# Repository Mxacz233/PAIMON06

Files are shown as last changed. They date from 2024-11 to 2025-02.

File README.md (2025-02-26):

<div style="flex: 1; text-align: center;">
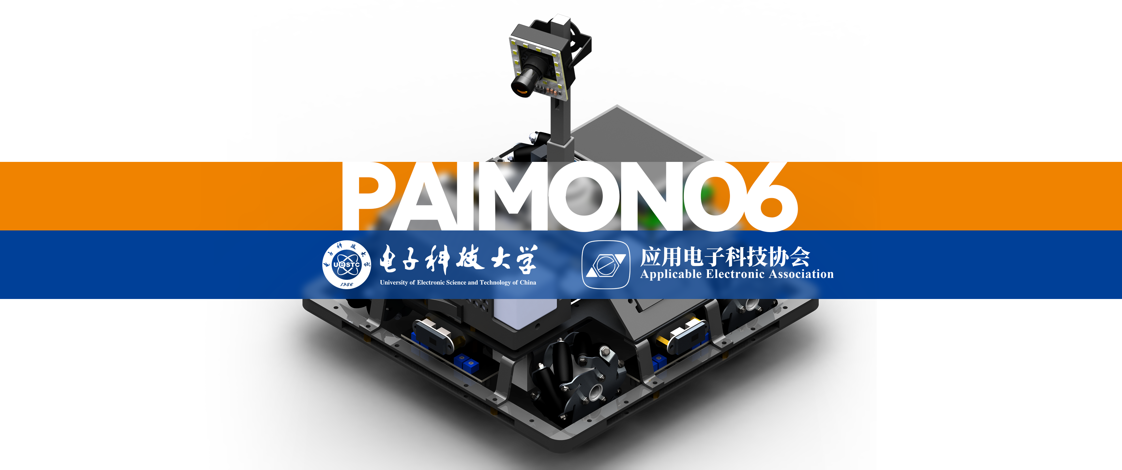
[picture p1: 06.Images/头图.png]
head
  
</div>

# PAIMON06: 高性能迷宫车










一辆全国一等奖的全部！从车上的每一颗螺丝到烧录文件的每一位HEX数据，全都在这里！

此项目是电子科技大学应用电子科技协会第十一届全国大学生光电设计竞赛（2023年）参赛作品，在西南赛区取得了第一名的成绩并在哈尔滨工业大学主办的全国总决赛中取得了全国一等奖的成绩。此项目包含了我们的全部的电路工程、全车建模、包含开发历史的软件与固件等信息。

*注意！此项目涉及嵌入式linux、嵌入式STM32、PCB设计、SolidWorks建模、Python脚本等多个领域，总文件可能较大(约650M)，建议根据需求按模块下载。*

*如果这个项目能够帮到你，请给我们一个Star⭐！如果你有任何问题或者建议，请在Issues中提出（bilibili私信不怎么看），我们会尽快回复！*

## 🌟 团队成员
<table border="0" style="border:none; margin-left:0;">
  <tr>
    <td align="center">
      <a href="https://github.com/RC-Wu">
        RC-Wu Avatar
        <br />
        <b>RC-Wu</b>
      </a>
    </td>
    <td align="center">
      <a href="https://github.com/Mxacz233">
        Mxacz233 Avatar
        <br />
        <b>Mxacz233</b>
      </a>
    </td>
    <td align="center">
      <a href="https://github.com/JimHans">
        JimHans Avatar
        <br />
        <b>JimHans</b>
      </a>
    </td>
  </tr>
</table>

## 🗃️ 文件介绍
文件介绍部分将简短介绍项目的工程组成，并给出一份功能表格方便查阅。
### 01.Software/软件部分：
由[JimHans](https://github.com/JimHans)同学开发，软件部分是多个涉及决策的`Python`脚本，部署在Rock PI 4C+上。
|程序|功能|
|:-:|:-:|
|点位识别|通过摄像头识别藏宝图中的宝藏点位|
|路径规划|根据识别的宝藏点位规划路径|
|动态路径更新|根据宝藏分布规律在运行中优化路径|
|静态化预编译|基于Cython的预编译|
### 02.Firmware/固件部分：
由[RC-Wu](https://github.com/RC-Wu)同学开发，固件部分是利用`CubeMX`和`KeilV5`联合开发的STM32固件，是一个完整工程。固件负责将上位机的决策信息传递给执行机构。
|品牌与型号|类型|内容|
|:-:|:-:|:-:|
|DJI M2006电机|无刷电机|CAN通信驱动|
|瓴控云台电机|无刷电机|CAN通信驱动|
|BOSCH BMI088|陀螺仪|SPI通信驱动|
|NOOPLOOP激光测距|激光测距|UART-DMA通信驱动|
|-|通信协议|上下位机UART-DMA通信协议|
### 03.CircuitBoard/电路部分：
由[Mxacz233](https://github.com/JimHans)同学开发，电路部分是利用`Altium Designer`设计的电路板，是五个完整工程，包含核心小板、陀螺仪小板、主板、电源板、分电板五个工程。电路部分均是高度定制化的PCB，为整车集成度提供了大量的贡献。
|品牌与型号|类型|内容|
|:-:|:-:|:-:|
|STM32F407|核心小板|电路设计方案|
|BMI088|陀螺仪小板|电路设计方案|
|-|主板|电路设计方案|
|TPS54360|电源管理|电路设计方案|
|-|分电板|电路设计方案|
### 04.Structure/机械部分：
由[Mxacz233](https://github.com/JimHans)同学开发，机械部分是利用`SolidWorks`设计的机械结构，是由多个.sldprt或.sldasm的子部件和一个整体的.sldasm总装配体组成的工程。机械部分是开发阶段对集成的考虑，使得全车紧凑装配成为可能。
|品牌与型号|类型|内容|
|:-:|:-:|:-:|
|DJI M2006电机+C610电调|无刷电机+电驱|最小驱控单元设计方案|
|格氏 6S航模电池|锂电池|含电压和开关的电池座设计方案|
|-|全车|机械设计方案|
## 📜 竞赛题目
### 1. 题目描述
#### 道具
- `场地`：一个4m×4m，10单元格×10单元格的迷宫中，随机选择8个单元格放置8块宝藏，每个单元格非联通边有隔板，地面有黑色循迹线。
- `藏宝图`：一张打印在A4纸上的迷宫缩略图，含有宝藏的单元格中心有黑色的点。
- `宝藏`：由红色或蓝色的积木贴上黄色圆形和绿色三角形组成，共八块

  |颜色|标签|类型|数量|
  |:-:|:-:|:-:|:-:|
  |红色|绿色三角形|红方真宝藏|3|
  |红色|黄色圆形|红方假宝藏|1|
  |蓝色|黄色圆形|蓝方真宝藏|3|
  |蓝色|绿色三角形|蓝方假宝藏|1|

<div style="flex: 1; text-align: center;">
  <table style="width:100%; border-collapse: collapse;">
  <td style="width:33.33%; text-align:center; padding:5px;">
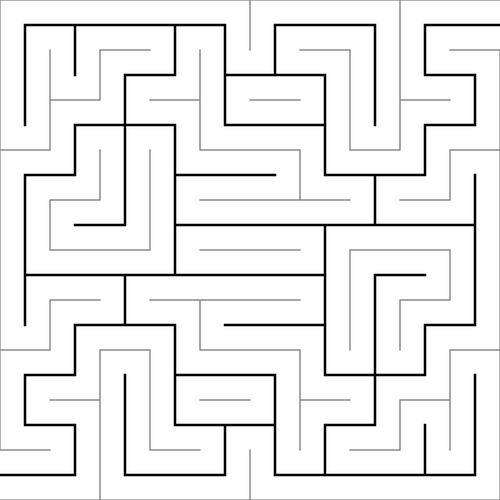
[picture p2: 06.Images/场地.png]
场地
    <br>
    <div>场地</div>
  </td>
  <td style="width:33.33%; text-align:center; padding:5px;">
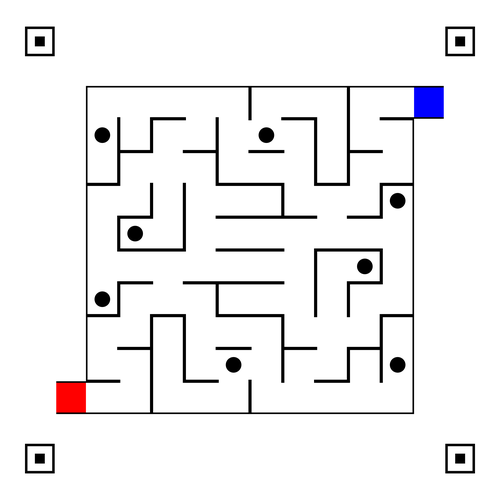
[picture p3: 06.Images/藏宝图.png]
藏宝图
    <br>
    <div>藏宝图</div>
  </td>
  <td style="width:33.33%; text-align:center; padding:5px;">
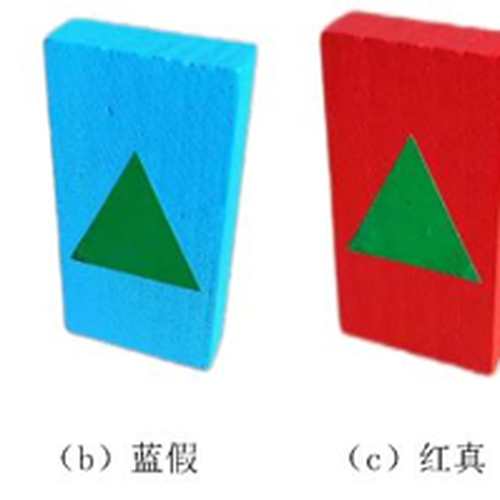
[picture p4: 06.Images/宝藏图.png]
宝藏
    <br>
    <div>宝藏</div>
  </td>
  </table>
</div>

#### 参赛车辆
参赛车辆有如下要求
- 尺寸合规
- 不得搭载恶意攻击功能
- 有限人工干涉，即从开始到完赛只能有放置车辆在场地入口、一键拍摄藏宝图、一键启动三次人工干涉
#### 抽象概念
- `阵营颜色`：由红色和蓝色两种颜色，分别代表红方和蓝方，一般由抽取决定。
- `识别正确数`：车辆碰倒己方真宝藏时，正确识别书加一。未碰倒宝藏、碰倒己方假宝藏、碰倒对方宝藏均不计入，并有对应惩罚。
- `完赛用时`：车辆从开始计时到抵达出口的时间。
### 2. 赛制规则
以下是一些和赛制规则相关的名词： 
- `积分赛`：单车计时赛，随机抽取`藏宝图`和`阵营颜色`，根据`完赛用时`和`识别正确数`综合打分。
- `对抗赛`：双车对抗赛，双方根据先后手分别抽取`藏宝图`和`阵营颜色`，在`识别正确数`相同的情况下，`完赛用时`较短的一方获胜，同时有一套双车纠缠重置规则。对抗赛进行两轮，每轮淘汰一半队伍，最终决出16支队伍进入全国总决赛。

西南赛区区赛采用`积分赛`+`对抗赛`的赛制：积分赛进行一轮，选择前64名进入对抗赛。对抗赛进行两轮，每轮淘汰一半队伍，最终决出16支队伍进入全国总决赛。

全国赛采用`对抗赛`的赛制：第一轮`对抗赛`在晋级一半队伍的基础上，参考积分赛规则根据赛中表现选择一部分未晋级队伍进行`对抗赛`，胜者与第一轮`对抗赛`晋级队伍共同参加第二轮`对抗赛`；第二轮`对抗赛`获胜的队伍获得全国一等奖。

### 3. 实况
- 校赛：成绩还可以，但是跑一半轮子掉了，真是令人贻笑大方。
- 西南赛区积分赛：识别正确数为3，满分，完赛用时为53秒，小计排名第二，第一名是重庆邮电大学的队伍，很强大，可惜因方案过于激进在对抗赛中失误。
- 西南赛区第一轮对抗赛：顺利完赛，但对手车辆出现问题，直至我方完赛仍未启动。
- 西南赛区第二轮对抗赛：对手车辆在第一轮对抗赛中出现问题，弃权。
- 全国赛第一轮对抗赛：对方为国防科技大学的队伍，对方车辆在直线行进速度优于我方，但转弯与识别速度不及我方，同时对方车辆在行进中出现失控，而后导致双方纠缠，最终我方险胜。
- 全国赛第二轮对抗赛：对方为广州大学的队伍，也是东南赛区区赛榜首，私下被戏称“东南top1vs西南top1”，竞赛中双方表现都十分优秀，后我方在时间上险胜，获得全国一等奖。
## 🛠️ 作品介绍
<div style="flex: 1; text-align: center;">
  <table style="width:100%; border-collapse: collapse;">
    <tr>
      <style="width:50%; text-align:center; padding:5px;">
        部件图<br>
        <div>部件图</div>
    </tr>
  </table>
</div>

1. 云台：由一个YAW轴云台电机、含碳纤维PLA打印法兰盘与支架、摄像头、摄像头补光灯小板组成，能够让摄像头始终朝向行进方向，便于第一时间识别。
2. 运动组：由四组运动单元组成，每组运动单元分别有麦克纳姆轮、M2006电机、C610电调各一个。集成后的运动单元使用XT30 2+2接口引出并连接至底层分电板。
3. 控制组：由一块触摸屏、一块ROCK PI 4C+，一块与ROCK PI 4C+尺寸与孔位相同，供电、信号接口对应的主板构成的三明治结构，集成后的控制组引出一个TypeC供电连接至电源板和30pinFPC排线连接至底层分电板。
4. 电源组：由电池组、电池、和一块电源板组成，电池组可以实时查看电池电压，避免欠压；电源可以快速更换；电源板将电池分为需要的电压和接口传递至底层分电板和主板。
5. 保险杠组：由铝方管、钣金裙甲、含碳纤维PLA打印转角组成，能够有效撞倒宝藏，同时避免与场地和对方车辆碰撞导致的内部损坏。
6. 传感器组：由四组传感单元组成，每组传感单元分别有四路灰度传感器、激光距离传感器各一个，能够后反馈四个方向的距离和地面路线。

综上，本作品其实不存在功能意义上的正面，任何一个方向均可完成前进与识别功能。作品从根本上消除了迷宫中转向所需要的大量时间，这种构型为取得优异成绩提供了大量帮助。

## 🏞️ 画廊

<div style="flex: 1; text-align: center;">
  <table style="width:100%; border-collapse: collapse;">
    <tr>
      <td style="width:33.33%; text-align:center; padding:5px;">
        第一代角度锁定测试<br>
        <div>第一代角度锁定测试</div>
      </td>
      <td style="width:33.33%; text-align:center; padding:5px;">
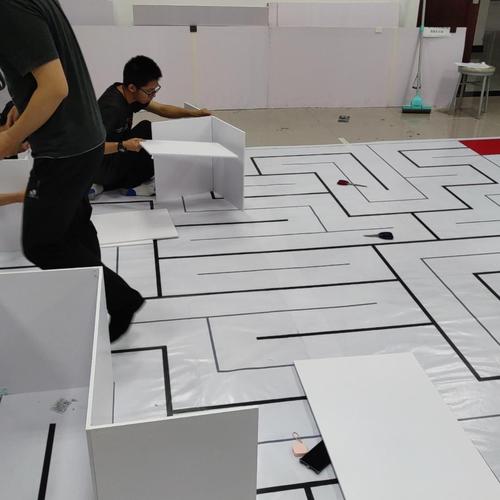
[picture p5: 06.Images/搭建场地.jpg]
搭建校内场地
        <br>
        <div>搭建校内场地</div>
      </td>
      <td style="width:33.33%; text-align:center; padding:5px;">
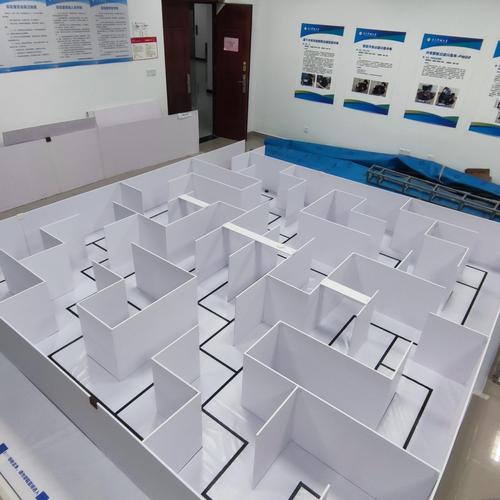
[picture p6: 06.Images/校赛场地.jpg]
搭建好的校内场地
        <br>
        <div>搭建好的校内场地</div>
      </td>
    </tr>
    <tr>
      <td style="width:33.33%; text-align:center; padding:5px;">
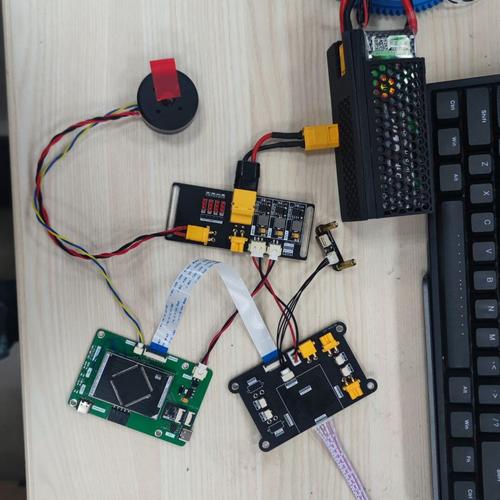
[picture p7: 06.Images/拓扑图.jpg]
电源板、控制板和分电板
        <br>
        <div>电源板、控制板和分电板</div>
      </td>
      <td style="width:33.33%; text-align:center; padding:5px;">
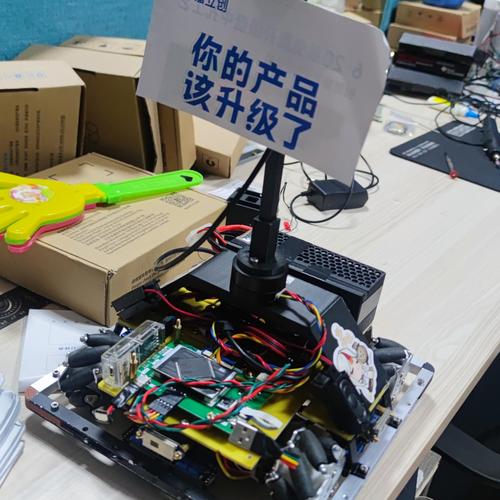
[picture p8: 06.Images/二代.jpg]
第二代，增加了理线，定制集成单元和原神贴纸
        <br>
        <div>第二代，理线、集成、原神贴纸</div>
      </td>
      <td style="width:33.33%; text-align:center; padding:5px;">
        二代角度摄像头锁定测试<br>
        <div>二代摄像头锁定测试</div>
      </td>
    </tr>
    <tr>
      <td style="width:33.33%; text-align:center; padding:5px;">
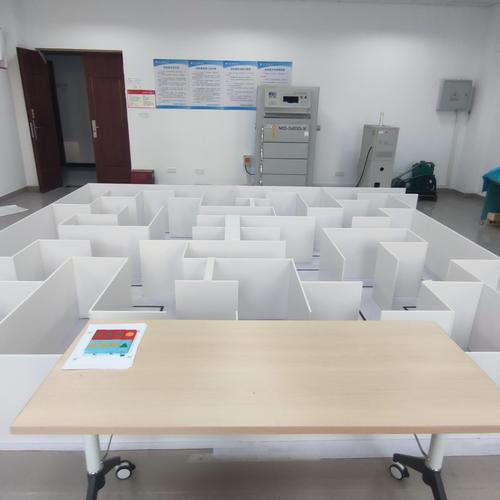
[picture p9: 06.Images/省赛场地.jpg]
省赛场地
        <br>
        <div>省赛场地</div>
      </td>
      <td style="width:33.33%; text-align:center; padding:5px;">
        第三代，碳板、黑色打印件并统一喷了黑色漆<br>
        <div>第三代，碳板、黑色件、黑色漆</div>
      </td>
      <td style="width:33.33%; text-align:center; padding:5px;">
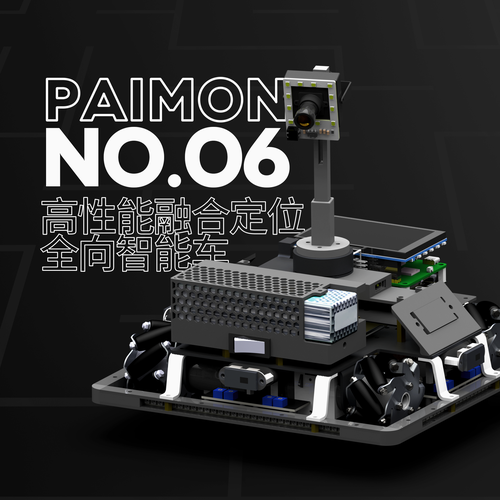
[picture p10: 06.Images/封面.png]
bilibili视频封面
        <br>
        <div>bilibili视频封面</div>
      </td>
    </tr>
    <tr>
      <td style="width:33.33%; text-align:center; padding:5px;">
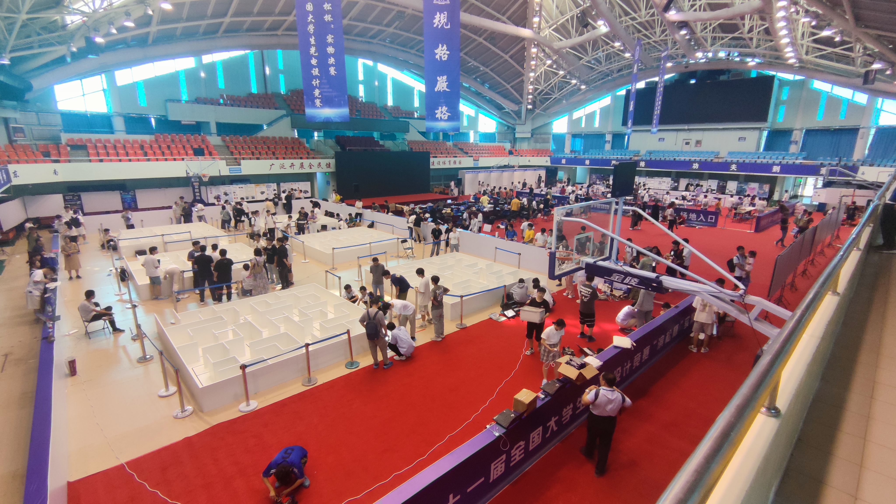
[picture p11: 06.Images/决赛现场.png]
决赛现场
        <br>
        <div>决赛现场</div>
      </td>
      <td style="width:33.33%; text-align:center; padding:5px;">
        颁奖典礼<br>
        <div>颁奖典礼</div>
      </td>
      <td style="width:33.33%; text-align:center; padding:5px;">
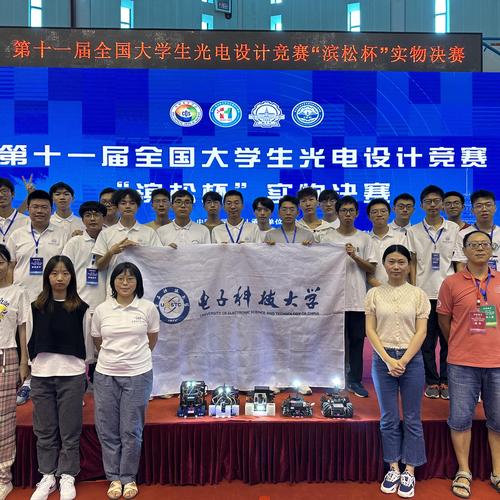
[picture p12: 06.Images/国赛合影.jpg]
国赛合影
        <br>
        <div>国赛合影</div>
      </td>
    </tr>
    <tr>
      <td style="width:33.33%; text-align:center; padding:5px;">
        吃了蘸酱菜辣椒而面露难色的队友<br>
        <div>吃了蘸酱菜辣椒而面露难色的队友</div>
      </td>
      <td style="width:33.33%; text-align:center; padding:5px;">
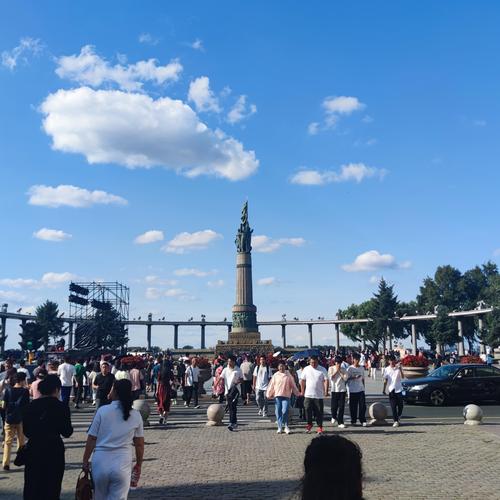
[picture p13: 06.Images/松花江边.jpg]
松花江边
        <br>
        <div>松花江边</div>
      </td>
      <td style="width:33.33%; text-align:center; padding:5px;">
        圣索菲亚大教堂<br>
        <div>圣索菲亚大教堂</div>
      </td>
    </tr>
  </table>

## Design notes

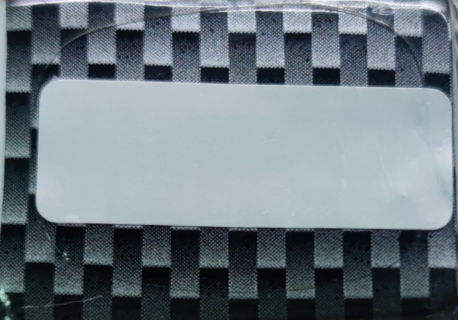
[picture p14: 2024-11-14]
04.Structure/电池/bottom.png

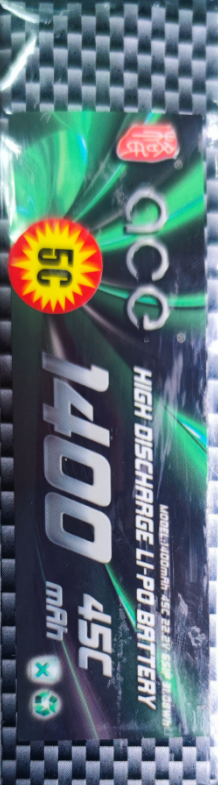
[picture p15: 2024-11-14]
04.Structure/电池/Top.png

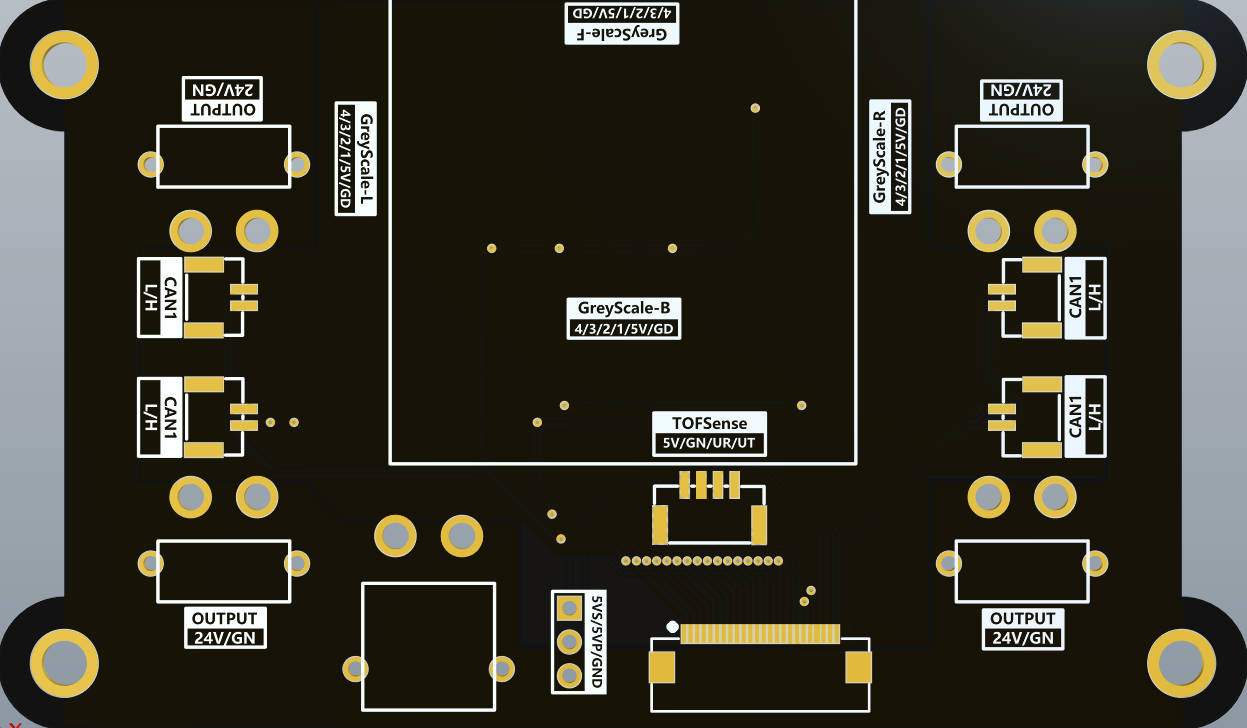
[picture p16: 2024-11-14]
04.Structure/底层中央板/PasteA.jpg

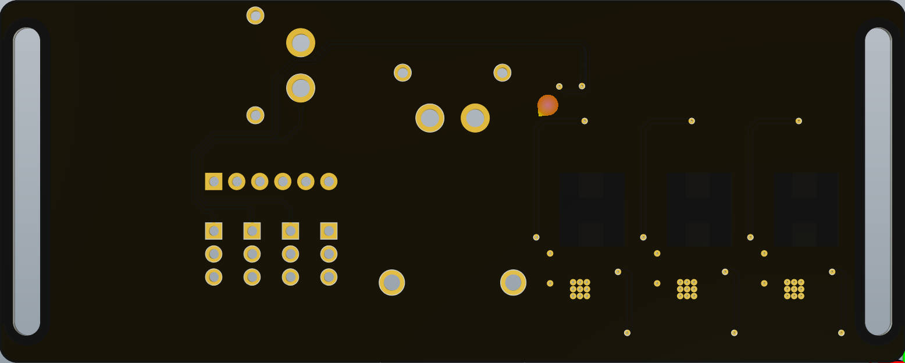
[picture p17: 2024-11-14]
04.Structure/电源板/PasteB.jpg

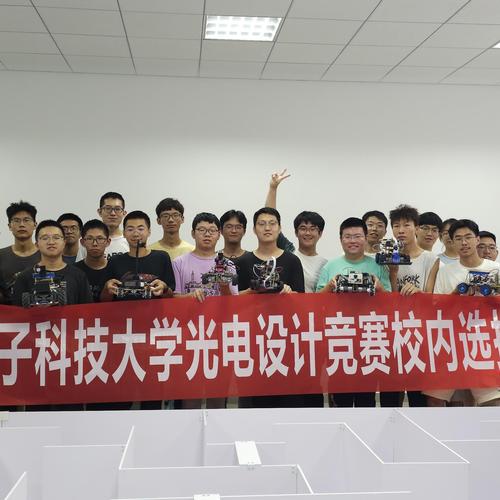
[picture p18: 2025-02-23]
06.Images/校赛合影.jpg

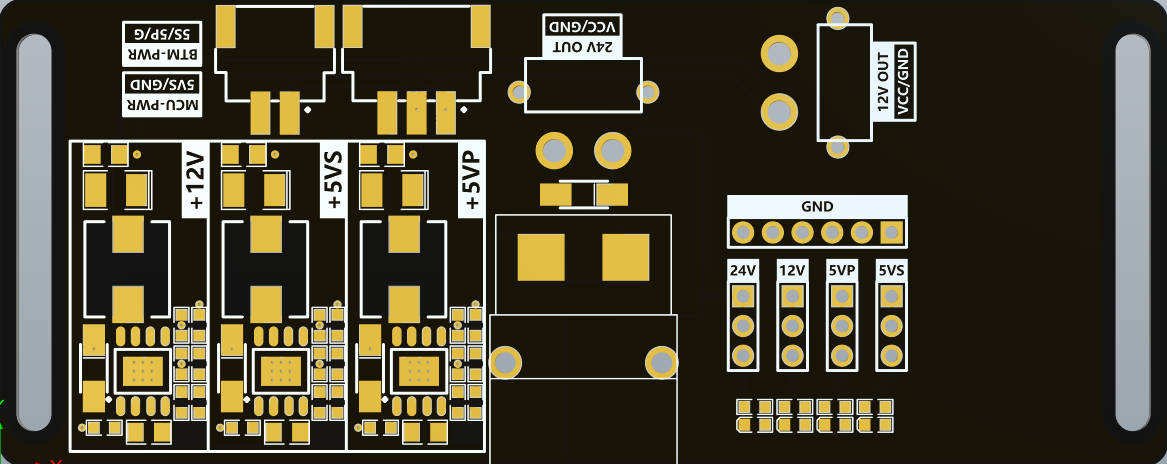
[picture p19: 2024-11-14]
04.Structure/电源板/PasteA.jpg

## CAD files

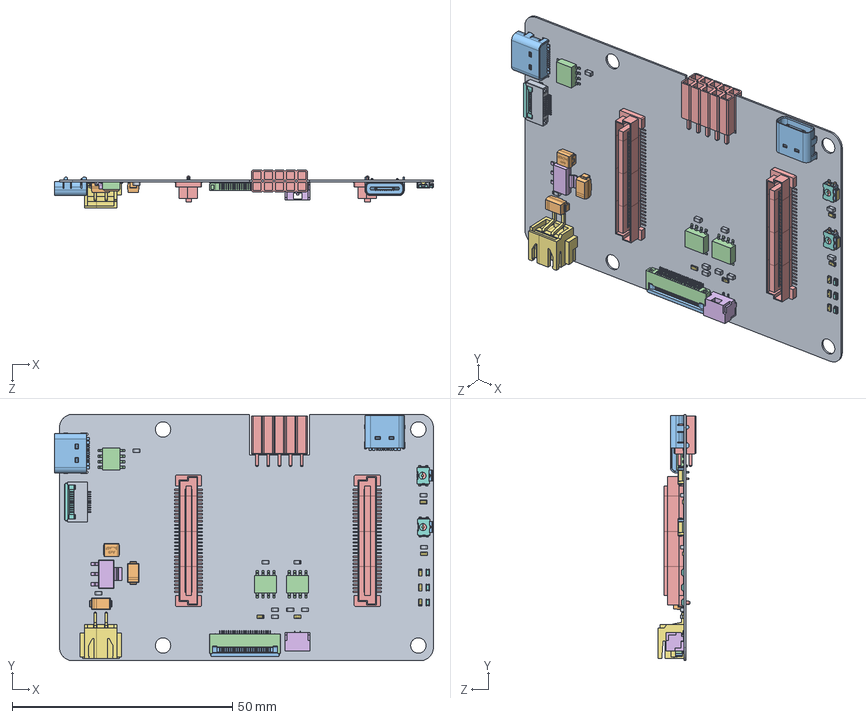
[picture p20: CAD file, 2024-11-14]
04.Structure/处理单元/核心板载板-V1.SLDASM
86.1 x 56.0 x 8.72 mm
User_Library-DO-214AC_SMA.step x 2
User_Library-USB_Type_C_Port_(SMD_Type).step x 2
SOIC8E_MPS.step x 3
BTB-60P-F.step x 2
ALSRobot-SOT223.step
User_Library-Res-0603.step x 7
6_1_2_3_4_5_600.step
7_1_2_3_4_5_6_A.step
FPC0_5_2H-W__1_2_30004.step x 10
6_1_2_3_4_5_6_7_8_0012.step
7_1_2_3_4_5_6_7_8_0016.step
FPC0_5_2H-W__1_2_30018.step x 24
User_Library-GH-2-90.step
XH2.54_AW_2P.step
ALSRobot-LED0603(G).step x 3
User_Library-c0603-3.step x 10
User_Library-AVX_BCASE.step
User_Library-KMS231G_Face.step x 2
User_Library-KMS231G_Face007.step x 2
User_Library-KMS231G_Face018.step x 2
User_Library-KMS231G_Face012.step x 2
User_Library-KMS231G_Face013.step x 2
User_Library-KMS231G_Face363.step x 2
User_Library-KMS231G_Face364.step x 2
User_Library-KMS231G_Face365.step x 2
User_Library-KMS231G_Face366.step x 2
User_Library-KMS231G_Face367.step x 2
User_Library-KMS231G_Face368.step x 2
User_Library-KMS231G_Face369.step x 2
User_Library-KMS231G_Face370.step x 2
User_Library-KMS231G_Face371.step x 2
User_Library-KMS231G_Face372.step x 2
User_Library-KMS231G_Face373.step x 2
User_Library-KMS231G_Face374.step x 2
User_Library-KMS231G_Face375.step x 2
User_Library-KMS231G_Face376.step x 2
User_Library-KMS231G_Face377.step x 2
User_Library-KMS231G_Face378.step x 2
User_Library-KMS231G_Face379.step x 2
User_Library-KMS231G_Face380.step x 2
User_Library-KMS231G_Face381.step x 2
User_Library-KMS231G_Face382.step x 2
User_Library-KMS231G_Face383.step x 2
User_Library-KMS231G_Face384.step x 2
User_Library-KMS231G_Face385.step x 2
User_Library-KMS231G_Face386.step x 2
User_Library-KMS231G_Face387.step x 2
User_Library-KMS231G_Face036.step x 2
User_Library-KMS231G_Face039.step x 2
User_Library-KMS231G_Face040.step x 2
User_Library-KMS231G_Face043.step x 2
User_Library-KMS231G_Face044.step x 2
User_Library-KMS231G_Face045.step x 2
User_Library-KMS231G_Face046.step x 2
User_Library-KMS231G_Face047.step x 2
User_Library-KMS231G_Face048.step x 2
User_Library-KMS231G_Face049.step x 2
User_Library-KMS231G_Face050.step x 2
User_Library-KMS231G_Face051.step x 2
User_Library-KMS231G_Face052.step x 2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

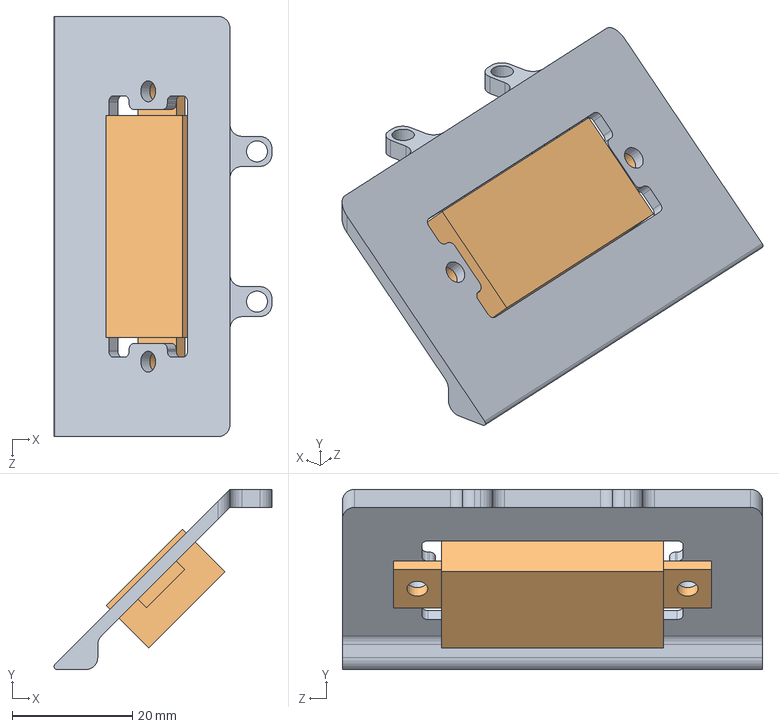
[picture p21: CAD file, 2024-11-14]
04.Structure/音响架/音响架.SLDASM
36.3 x 30.0 x 70.0 mm
裙甲
音响

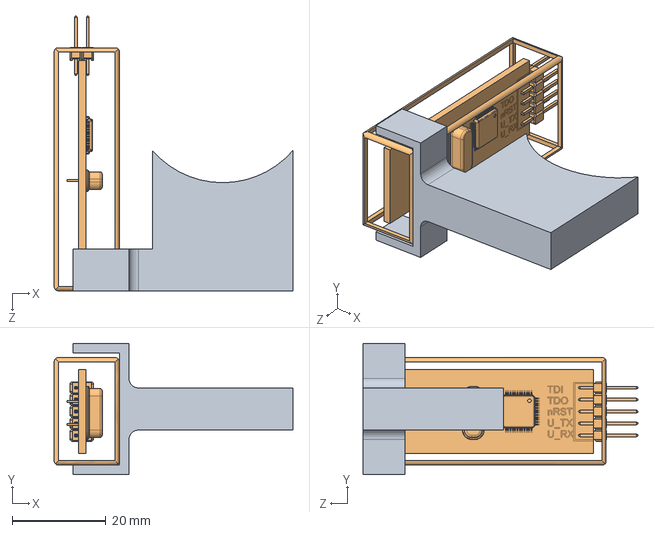
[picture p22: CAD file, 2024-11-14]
04.Structure/烧录组/烧录组.SLDASM
51.0 x 28.0 x 58.7 mm
DAP支架
DAP

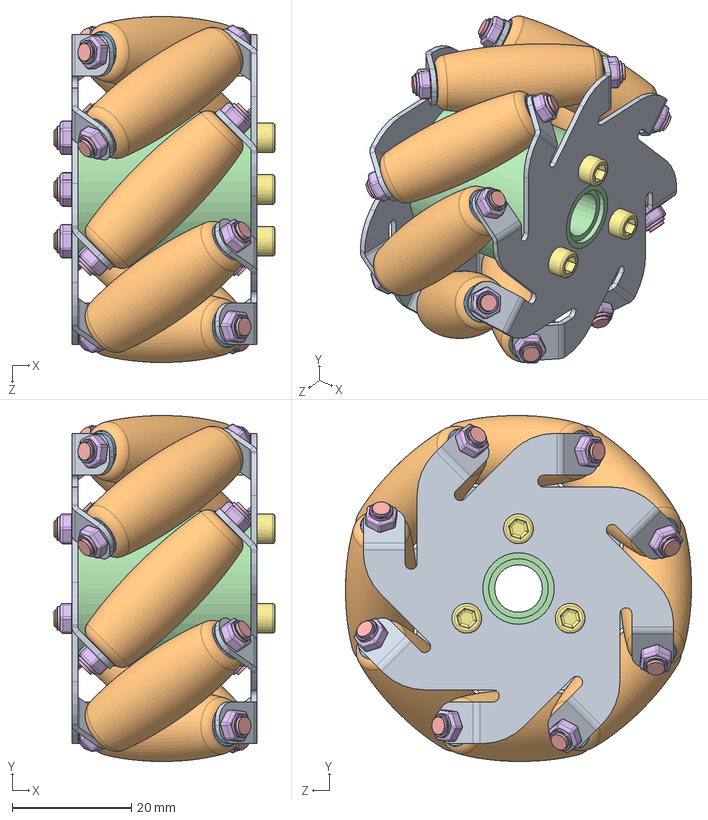
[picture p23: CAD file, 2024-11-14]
04.Structure/麦轮/60mm右旋麦轮.SLDASM
37.0 x 58.0 x 58.0 mm
plate_2 x 2
roller x 8
liner x 16
inner_cylinder
two_sided_screw x 8
3mm_bolt x 19
3x35_screw x 3

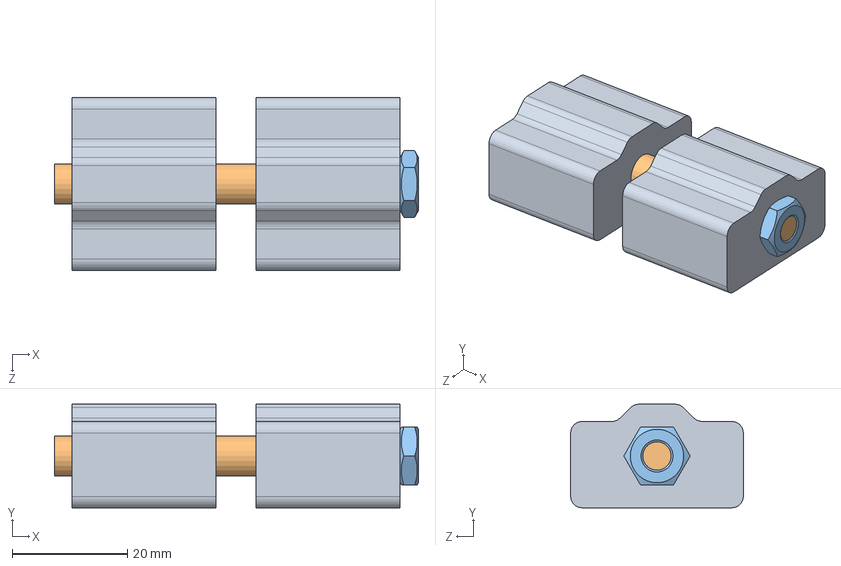
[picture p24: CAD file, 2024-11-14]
04.Structure/共轴悬挂/共轴悬挂.SLDASM
63.2 x 18.0 x 30.0 mm
共轴悬挂-单侧 x 2
共轴悬挂-主轴
hex thin nuts-grades ab-chamfered gb

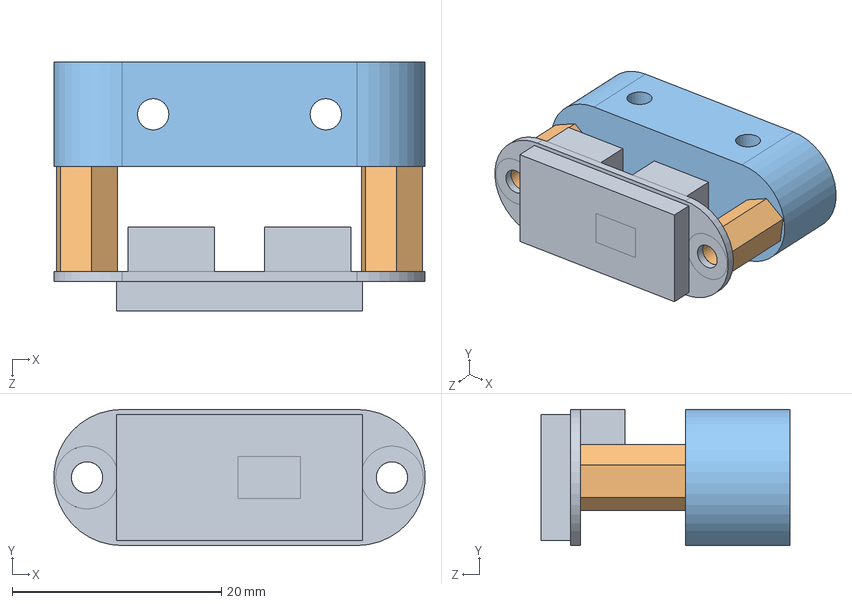
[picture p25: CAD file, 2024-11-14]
04.Structure/测距单元/测距单元.SLDASM
35.5 x 13.0 x 23.8 mm
TOFSenseP
M3-10mm铜柱 x 2
测距支架

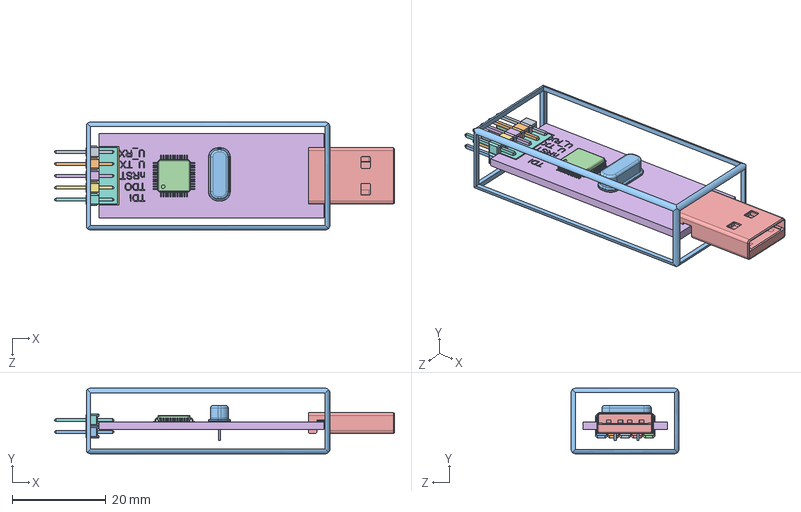
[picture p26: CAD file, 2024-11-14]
04.Structure/烧录组/DAP.SLDASM
72.5 x 14.0 x 23.0 mm
User Library-1x2 TH Pitch 2_54mm.step
User Library-1x2 TH Pitch 2_54mm (1).step
User Library-1x2 TH Pitch 2_54mm (2).step
User Library-1x2 TH Pitch 2_54mm (3).step
User Library-1x2 TH Pitch 2_54mm (4).step
User Library-1x2 TH Pitch 2_54mm (5).step
User Library-1x2 TH Pitch 2_54mm (6).step
User Library-1x2 TH Pitch 2_54mm (7).step
User Library-1x2 TH Pitch 2_54mm (8).step
User Library-1x2 TH Pitch 2_54mm (9).step
直插晶振 v1.step
LQFP-48 v2.step
无标题.step
无标题-0.step
无标题-1.step
无标题-2.step
无标题-3.step
无标题-4.step

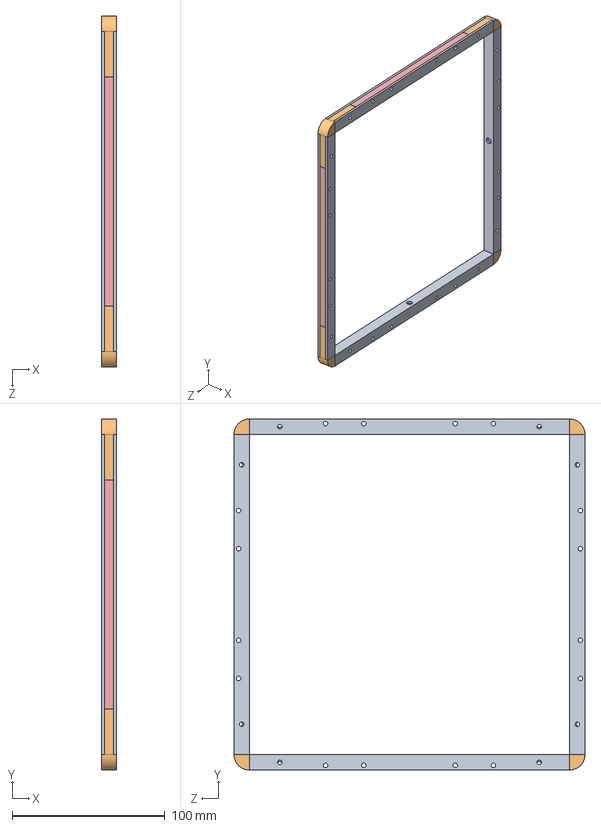
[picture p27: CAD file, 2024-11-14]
04.Structure/保险杠/保险杠.SLDASM
10.0 x 230.0 x 230.0 mm
保险杠-单杠 x 4
保险杠-衔接 x 4
PM06-保险杠灯-V1.step x 4
M3-0+6铜柱 x 8
均光板 x 4

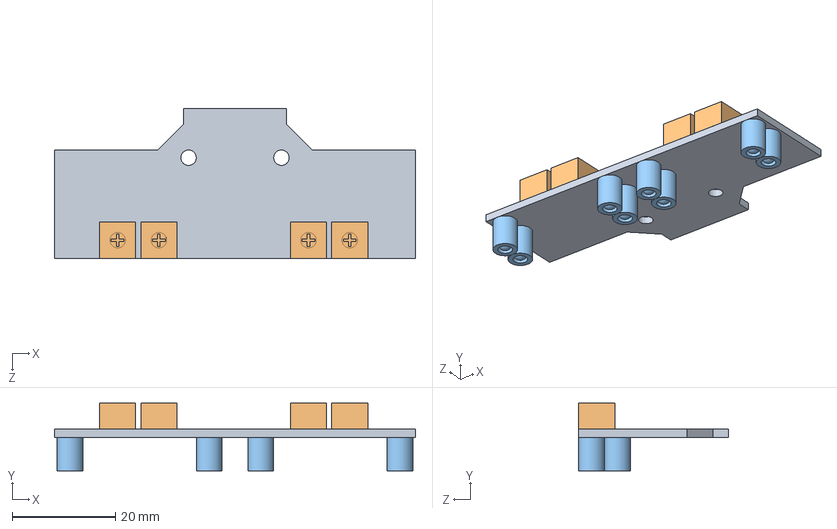
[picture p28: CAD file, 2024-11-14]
04.Structure/巡线模块/巡线模块.SLDASM
70.0 x 13.1 x 29.0 mm
巡线模块-基板
巡线模块-电位器 x 4
巡线模块-探头 x 4

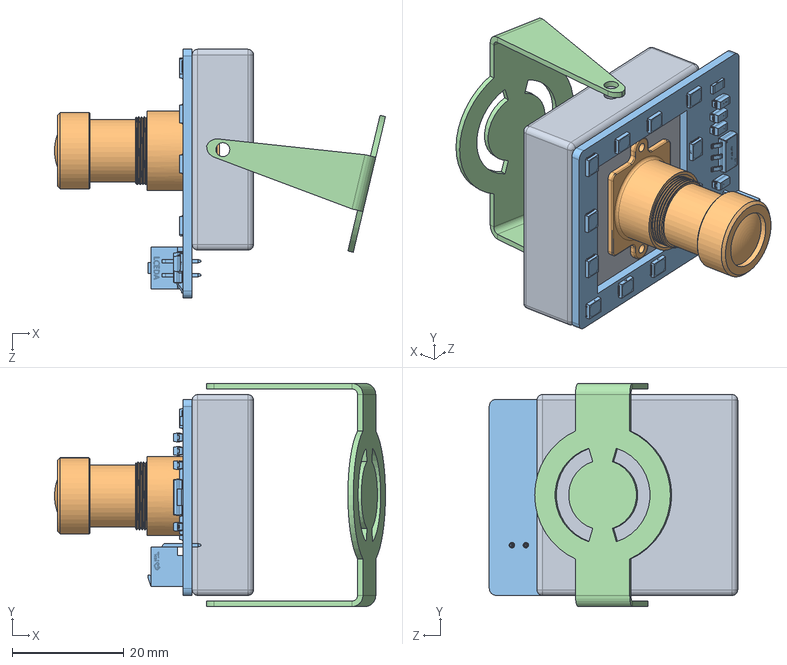
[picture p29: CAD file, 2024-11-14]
04.Structure/摄像头组/摄像头组.SLDASM
59.3 x 40.0 x 44.6 mm
摄像头外壳
摄像头
摄像头补光板
摄像头支架

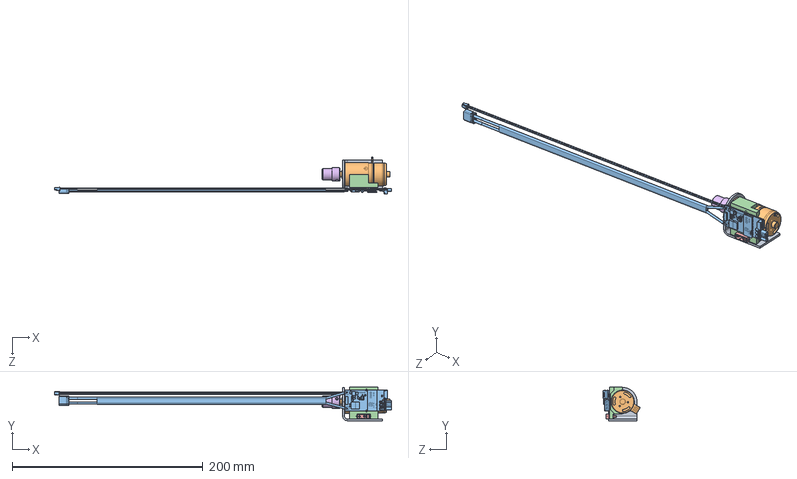
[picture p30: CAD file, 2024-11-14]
04.Structure/运动单元/运动单元-俯视副对角线.SLDASM
353.3 x 35.2 x 38.8 mm
M2006电机支架-V1
M2006电机
C610无刷电机调速器
电调支架-俯视副对角线
XT30(2+2)
联轴器

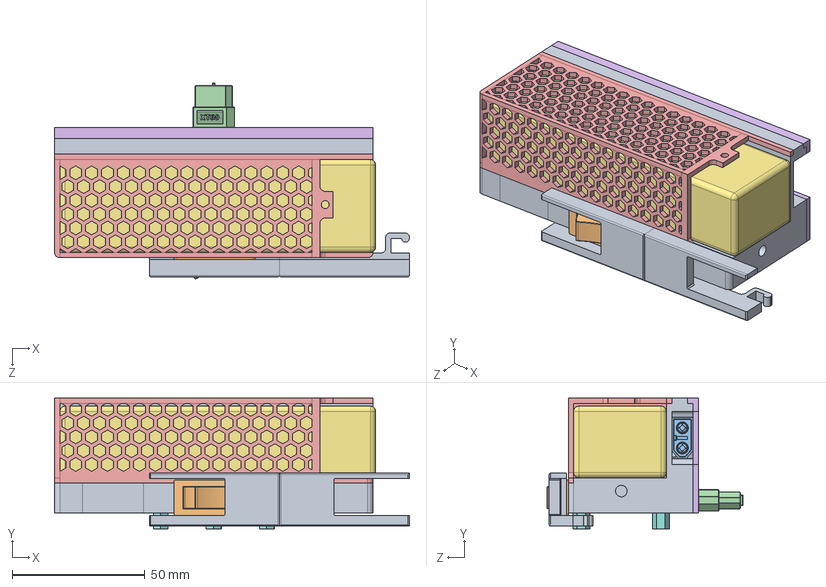
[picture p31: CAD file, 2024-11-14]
04.Structure/电池/电池仓.SLDASM
133.8 x 49.2 x 73.8 mm
电池舱主体、
KCD3船型开关
XT60
XT60母
电池仓外壳
电池仓盖板
电池
M3-6mm铜柱 x 3
开关锁
表头载板
电压表数码管

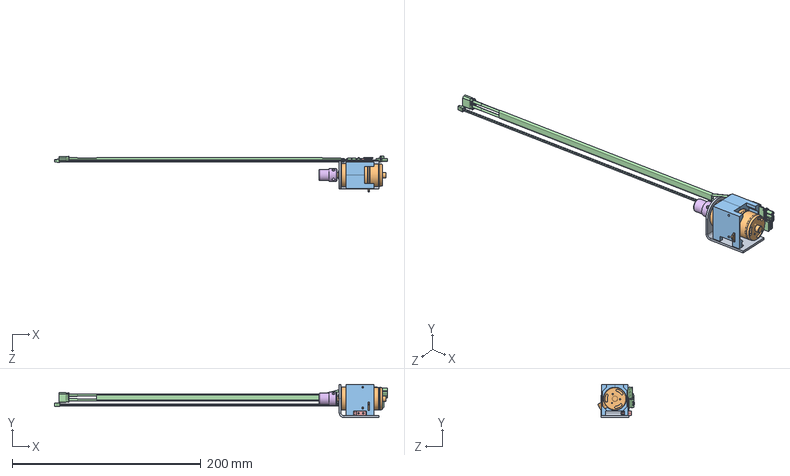
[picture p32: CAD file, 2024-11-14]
04.Structure/运动单元/运动单元-俯视主对角线.SLDASM
353.3 x 35.2 x 38.6 mm
M2006电机支架
M2006电机
电调支架-俯视主对角线
C610无刷电机调速器
XT30(2+2)
联轴器

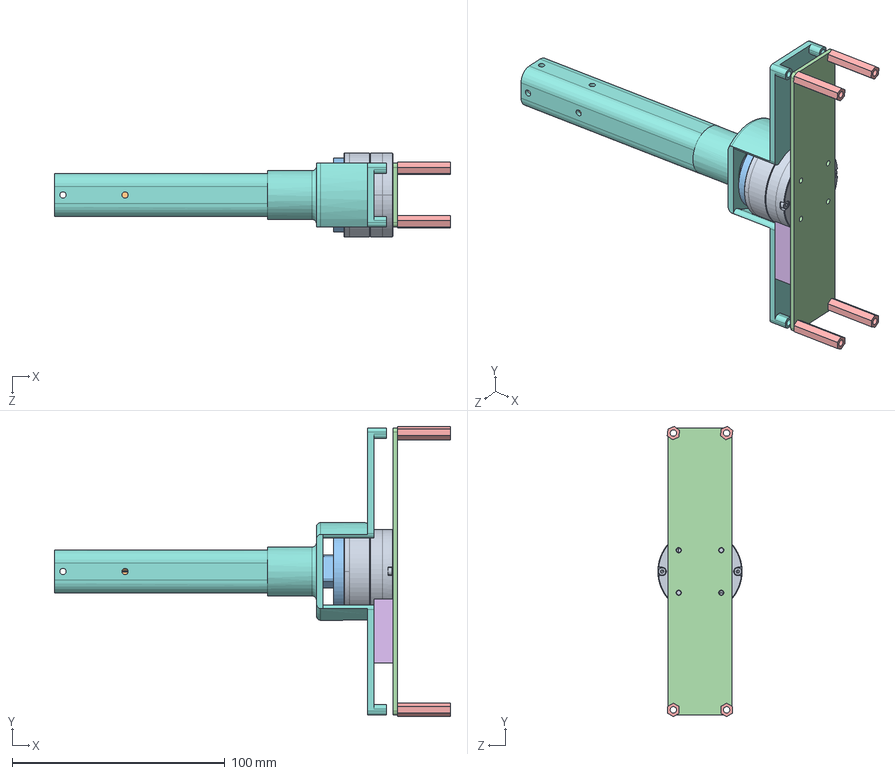
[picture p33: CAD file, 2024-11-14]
04.Structure/云台组/云台组.SLDASM
186.0 x 136.3 x 39.6 mm
MS4005云台电机
摄像头杆
摄像头座
云台小板
M3-25mm铜柱 x 4
云台转接盖
XT30(2+2)
激光架

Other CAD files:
04.Structure/电池/电池载板.SLDASM
04.Structure/麦轮/Mecanum_Wheel_60mm_Right_ASM_AP214.STEP
04.Structure/麦轮/Mecanum_Wheel_60mm_Left_ASM.SLDASM
04.Structure/麦轮/60mm左旋麦轮.SLDASM
04.Structure/云台组/M3-20mm铜柱.SLDPRT
04.Structure/云台组/MS4005云台电机.SLDPRT
04.Structure/云台组/XT30(2+2).SLDPRT
04.Structure/云台组/云台小板.SLDPRT
04.Structure/云台组/云台转接盖.SLDPRT
04.Structure/云台组/初始云台支架.SLDPRT
04.Structure/云台组/摄像头座.SLDPRT
04.Structure/云台组/摄像头杆.SLDPRT
04.Structure/云台组/激光架.SLDPRT
04.Structure/保险杠/M3-0+6铜柱.SLDPRT
04.Structure/保险杠/PM06-保险杠灯-V1.step
04.Structure/保险杠/保险杠-单杠.SLDPRT
04.Structure/保险杠/保险杠-支架.SLDPRT
04.Structure/保险杠/保险杠-衔接-适应实际尺寸缩小版.SLDPRT
04.Structure/保险杠/保险杠-衔接-适应实际尺寸缩小版.STL
04.Structure/保险杠/保险杠-衔接.SLDPRT
04.Structure/保险杠/保险杠灯.SLDPRT
04.Structure/保险杠/均光板.SLDPRT
04.Structure/共轴悬挂/共轴悬挂-主轴.SLDPRT
04.Structure/共轴悬挂/共轴悬挂-单侧.SLDPRT
04.Structure/处理单元/3.5寸屏幕.SLDPRT
04.Structure/对抗识别组/DOCK支架.SLDPRT
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

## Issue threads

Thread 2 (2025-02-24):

Regarding the issue of the lower computer program

zhengpangzi, 2025-02-24:
Hello senior, I am very interested in your project and have now replicated a similar car. I would like to inquire whether the lower computer program of the senior, which is the program on Keil, is open source. I would like to provide some driving control for the car. Thank you, senior.😊😊😊

Closed 2025-02-26.

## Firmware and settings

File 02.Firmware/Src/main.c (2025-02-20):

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
/* Includes ------------------------------------------------------------------*/
#include "main.h"
#include "can.h"
#include "dma.h"
#include "spi.h"
#include "tim.h"
#include "usart.h"
#include "gpio.h"

/* USER CODE BEGIN Includes */
#include "motor_control.h"
#include "PosLock.h"
#include "BMI088driver.h"
#include "KalmanFilter.h"
#include "AngleLock.h"
#include "Liner.h"
#include "bsp-protocol.h"
#include "lk_bsp_can.h"
#include "MS40X.h"
#include "math.h"
#include <stdio.h>
#include <string.h>
/* USER CODE END Includes */

/* USER CODE BEGIN PD */
#define mode_flag  2 		//0:主动输出模式   1:查询输出模式    2:级联模式
#define pi 3.1415926
#define StardardSpeed 11000
#define SlowStardardSpeed 6000  //处理特殊情况时的速度
#define INIT_DEGREE 5500        //别忘了bsp-protocol里还有一样的define
/* USER CODE END PD */


/* USER CODE BEGIN PV */
int32_t set_spd = 2000;
uint8_t DirFlag=0;

float dis1,dis2,dis3,dis4=0;

uint8_t TOF_ID = 1;			//仅用作级联时更改查询命令
uint8_t u_tx_buf[8] = {0x57,0x10,0xff,0xff,0x00,0xff,0xff,0x63};  //查询命令
uint8_t u_rx_buf[400];

uint32_t TOF_data_length=0;		//DMA接收数据长度
void TOFRefresh(void);

uint8_t flag=0;
uint8_t SlowSpeedFlag = 0;
//int32_t set_spd = normspeed;
int32_t tar = 90;
fp32 gyro[3], accel[3], temp;
double yaw=0;
float timeflag=0;
EularAngle_t EularAngle ={
	.yaw=0,
	.pitch=0,
	.roll=0
};
Liner_t Liner ={
	.left=0,
	.right=0,
	.front=0,
	.back=0,
};
Speed_t Speed={
	.speedx=0,
	.speedy=0,
	.speedw=0,
};
Speed_t speedcum={
  .speedx=0,
  .speedy=0,
  .speedw=0,
};
void Front(void);
void Back(void);
void Right(void);
void Left(void);
void AdpSpeedCon(char dir);
void SpeedCumulativeRun(Speed_t *speed,Liner_t *liner,char dir);
void SlowSpeedCumulativeRun(Speed_t *speed,Liner_t *liner,char dir);
void SpeedCumulativeBreak(Speed_t *speed,Liner_t *liner,char dir,char block);
void SlowSpeedCumulativeBreak(Speed_t *speed,Liner_t *liner,char dir,char block);
void SpeedCumulativeCirCle(Speed_t *speed,char dir,char nextdir,char block);
uint32_t TOFSignalFlag(char dir);
char InvDir(char dir);
uint8_t RuntoBreakFlag(char dir);
float BreaktoChangeFlag(char dir);
char map[400];
//char map[]="F0L0B0L0F0L0F0R0F1R0B0L0R0F0L0F0R0F1L0R0B1L0F0L0F0B0R1B0L2B0F0L0B0L1F0B0L0B1R0B0F0L0F0L0B1R0L0F0R1F1L0F0R0L0B0R0F0R0F0L0F0L0B0L0B2S0";
//char map[]="F2S0";'S'
//char map[]="FLS";
//char map_temp[]={"FF00LL00BB00LL00FF00LL00FF00RR20FF00RR20BB20RR00BB00LL20LL00RR00FF00LL02FF02LL00BB02FL20SS00"};
//------------------------------------------------|1-----------------------
//1号情况
//char map[]="BB00LR20SS00SS";
//2号情况
//char map[]="RR00LF00SS00SS";
//3号情况
//char map[]="LL00FB40SS00SS";
//4号情况
//char map[]="FF60LL20RB20SS00SS";
//5号情况
//char map[]="RR00LF00SS00SS";




char *RunFrame			=	map;
char *MapFrame			=	map+1;
char *BlockFrame		=	map+2;
char *ChangeDis			=	map+3;
char *NextMapFrame	=	map+4;

uint8_t left[4]={0};
uint8_t right[4]={0};
uint8_t front[4]={0};
uint8_t back[4]={0};
uint8_t PauseBlockFlag = 0;//暂停标志位
uint32_t AskNum = 0;//停止状态计数
uint32_t InitNum = 0;//初始状态计数
uint32_t tempRoadNum = 0;
uint32_t tempRoadNumNext = 0;

typedef enum
{
	MOTION_INIT=0,
	MOTION_START,
	MOTION_RUN,
	MOTION_BREAK,
	MOTION_CIRCLE,//圆弧插补
  MOTION_CHANGE,//换向状态
  MOTION_STOP,//停止状态
	MOTION_PAUSE,//暂停状态
}MOTION_STATE;
volatile double run2offflag=0;
volatile double changeflag=0;
volatile uint32_t startspeed=0;
MOTION_STATE MotionState = MOTION_INIT;
//MOTION_STATE MotionState = MOTION_OFFSET;

uint16_t motionflag=0;
/* USER CODE END PV */

void SystemClock_Config(void);
/**
  * @brief  The application entry point.
  * @retval int
  */
int main(void)
{
  /* MCU Configuration--------------------------------------------------------*/

  /* Reset of all peripherals, Initializes the Flash interface and the Systick. */
  HAL_Init();

  /* Configure the system clock */
  SystemClock_Config();

  /* Initialize all configured peripherals */
  MX_GPIO_Init();
  MX_DMA_Init();
  MX_SPI1_Init();
  MX_TIM10_Init();
  MX_CAN1_Init();
  MX_TIM11_Init();
  MX_USART3_UART_Init();
  MX_TIM2_Init();
  MX_TIM12_Init();
  MX_TIM13_Init();
  MX_CAN2_Init();
  MX_USART1_UART_Init();
  /* USER CODE BEGIN 2 */

//	/**@Communication */
	CommReceiveInit();
	

//	/**@IMU */
	while(BMI088_init()){};
	

//	/**@Motor */
	motor_init_4p();

//	/**@TOFSense */	
	//while(!(dis1||dis2||dis3||dis4)){};

//	/**@GreyScaleSensor */
	LineRead(&Liner);

//  /**@MS4005 */
	vApp_User_CAN_Configuration();
	
//	strncpy(map,map_temp,strlen(map_temp));
	__HAL_TIM_CLEAR_IT(&htim10,TIM_IT_UPDATE);
	__HAL_TIM_CLEAR_IT(&htim11,TIM_IT_UPDATE);
	__HAL_TIM_CLEAR_IT(&htim12,TIM_IT_UPDATE);
	__HAL_TIM_CLEAR_IT(&htim13,TIM_IT_UPDATE);
	HAL_TIM_Base_Start_IT(&htim10);
	HAL_TIM_Base_Start_IT(&htim11);
	HAL_Delay(3000);
	HAL_TIM_Base_Start_IT(&htim12);
	HAL_TIM_Base_Start_IT(&htim13);
	__HAL_UART_ENABLE_IT(&huart3,UART_IT_IDLE);	
	PlatformConAbsAng(INIT_DEGREE);
		
//	MotionState=MOTION_STOP;
////转换test
//	RoadsNumUpper = 3;
	
	
//	发送test
//	CheckTreasureFlag = 1;
  /* USER CODE END 2 */

  /* Infinite loop */
  /* USER CODE BEGIN WHILE */
  while (1)
  {
    /* USER CODE END WHILE */

    /* USER CODE BEGIN 3 */
	  protocol_analysis();

  }
  /* USER CODE END 3 */
}

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
/* USER CODE BEGIN 4 */
void HAL_TIM_PeriodElapsedCallback(TIM_HandleTypeDef *htim)
{	
	if(htim->Instance == TIM10)//200Hz
	{
		TOFRefresh();
	}	
	if(htim->Instance == TIM11)//1000Hz
	{
		BMI088_read(gyro, accel, &temp);
		EularAngle.accel[0]=accel[0];
		EularAngle.accel[1]=accel[1];
		EularAngle.accel[2]=accel[2];
		EularAngle.gyro[0]=gyro[0];
		EularAngle.gyro[1]=gyro[1];
		EularAngle.gyro[2]=gyro[2];
		YawSolve(&EularAngle);
		if(MotionState!=MOTION_INIT) yaw=EularAngle.yaw;
		LineRead(&Liner);
	}
	if(htim->Instance == TIM12)//100Hz
	{
		// 运动状态机
    switch (MotionState)
    {
      case MOTION_INIT://起始状态
      {
        // 执行200次
        motionflag++;
		
        if(motionflag>200 && RoadInfoFinishFlag == 1)//路段信息接收完成
        {
					EularAngle.yaw=0;
          motionflag=0;
          MotionState=MOTION_RUN;
        }
        break;
      }
		case MOTION_START://起始状态
    {
				if(*MapFrame=='L')
				{
					if(abs(Speed.speedy)>=SlowStardardSpeed || dis4<150+185*(*BlockFrame-'0'+1))
					{
						Speed.speedx=0;
						MotionState=MOTION_RUN;
					}
					Speed.speedx=-0;
					Speed.speedy-=200;
				}
				if(*MapFrame=='R')
				{
					if(abs(Speed.speedy)>=SlowStardardSpeed || dis2<150+185*(*BlockFrame-'0'+1))
					{
						Speed.speedx=0;
						MotionState=MOTION_RUN;
					}
					Speed.speedx=-0;
					Speed.speedy+=200;
				}
				break;
    }
    case MOTION_RUN://运动状态
    {
			RoadInfoFinishFlag = 0;		//路段信息接收完成标志位归零
//			if(SlowSpeedFlag==1)
//			{
//				SlowSpeedCumulativeRun(&speedcum,&Liner,*MapFrame);			
//			}	
//			else 
//			{	
//				SpeedCumulativeRun(&speedcum,&Liner,*MapFrame);
//			}
//			Speed.speedx=speedcum.speedx;
//			Speed.speedy=speedcum.speedy;
			//下面这个值在圆弧插补中加入了状态为4的情况，mark
			if((RuntoBreakFlag(*MapFrame)==0 || RuntoBreakFlag(*MapFrame)==4 || RuntoBreakFlag(*MapFrame)==11 || RuntoBreakFlag(*MapFrame)==12 ) 
				)//判断是否需要刹车
			{
				MotionState=MOTION_BREAK;

			}
			break;
    }
    case MOTION_BREAK://刹车状态
    {
//			if(SlowSpeedFlag==1)
//			{
//				SlowSpeedCumulativeBreak(&speedcum,&Liner,*MapFrame,*BlockFrame);		
//			}	
//			else 
//			{	
//				SpeedCumulativeBreak(&speedcum,&Liner,*MapFrame,*BlockFrame);
//			}
			SpeedCumulativeBreak(&speedcum,&Liner,*MapFrame,*BlockFrame);
			Speed.speedx=speedcum.speedx;
			Speed.speedy=speedcum.speedy;//之前的一格现在变成两格了！记得改！
//----------------------------------------8月1日版本--------------------------------------------------------------------------------------------------
//		  if(*NextMapFrame!='S' &&
////			if(*NextMapFrame!='S' && (*BlockFrame - '0') < 4 && 
//					(RuntoBreakFlag(*MapFrame)==0 || RuntoBreakFlag(*MapFrame)==4 || RuntoBreakFlag(*MapFrame)==11 || RuntoBreakFlag(*MapFrame)==12) && 
//					BreaktoChangeFlag(*MapFrame)<125+185*(*BlockFrame-'0'+1) &&
//					BreaktoChangeFlag(*MapFrame)>25+185*(*BlockFrame-'0'+1) &&
//			(InvDir(*NextMapFrame)!=*MapFrame && *NextMapFrame!=*MapFrame))//判断是否需要换向
//			{
//				MotionState=MOTION_CIRCLE;
//			}
//			//长距直接跳过圆弧
//			if( (*NextMapFrame=='S' || ((*ChangeDis) - '0') >= 8 ) &&
////			if( (*NextMapFrame=='S' || ((*ChangeDis) - '0') >= 8 || (*BlockFrame - '0') >= 6) &&
////			if( (*NextMapFrame=='S' || ((*ChangeDis) - '0') >= 6) &&
//					(RuntoBreakFlag(*MapFrame)==0 || RuntoBreakFlag(*MapFrame)==4 || RuntoBreakFlag(*MapFrame)==11 || RuntoBreakFlag(*MapFrame)==12) && 
//					BreaktoChangeFlag(*MapFrame)<150+185*(*BlockFrame-'0'))
//			{
//				MotionState=MOTION_CHANGE;
//			} 
//			//180度换向或者下一步前进时不改变方向的两种情况下直接跳过圆弧插补
//			if(*NextMapFrame!='S' &&
//				(RuntoBreakFlag(*MapFrame)==0 || RuntoBreakFlag(*MapFrame)==4 || RuntoBreakFlag(*MapFrame)==11 || RuntoBreakFlag(*MapFrame)==12) &&
//			(InvDir(*NextMapFrame)==*MapFrame || *NextMapFrame==*MapFrame) &&
//			BreaktoChangeFlag(*MapFrame)<150+185*(*BlockFrame-'0'))
//			{
//				MotionState=MOTION_CHANGE;
//			}
//----------------------------------------8月1日版本end-----------------------------------------------------------------------------------------------			

//----------------------------------------长距跳过圆弧版本---------------------------------------------------------------------------------------------	
			
			//=====================圆弧插补============================
			if(*NextMapFrame!='S' && (*BlockFrame - '0') < 6 && (*ChangeDis - '0') < 6 &&
					(RuntoBreakFlag(*MapFrame)==0 || RuntoBreakFlag(*MapFrame)==4 || RuntoBreakFlag(*MapFrame)==11 || RuntoBreakFlag(*MapFrame)==12) && 
					TOFSignalFlag(*MapFrame)>2 &&
					BreaktoChangeFlag(*MapFrame)<125+185*(*BlockFrame-'0'+1) &&
					BreaktoChangeFlag(*MapFrame)>10+185*(*BlockFrame-'0'+1) &&
					(InvDir(*NextMapFrame)!=*MapFrame && *NextMapFrame!=*MapFrame) &&
					*RunFrame == *MapFrame
				)//(排除掉撞击的情况)判断是否需要换向
			{
				SlowSpeedFlag = 0;//将慢速标志位归零
				MotionState=MOTION_CIRCLE;
			}
			
			
			
//			//长距直接跳过圆弧
//			if( (*NextMapFrame=='S' || ((*ChangeDis) - '0') >= 8 ) &&
////			if( (*NextMapFrame=='S' || ((*ChangeDis) - '0') >= 8 || (*BlockFrame - '0') >= 6) &&
////			if( (*NextMapFrame=='S' || ((*ChangeDis) - '0') >= 6) &&
//					(RuntoBreakFlag(*MapFrame)==0 || RuntoBreakFlag(*MapFrame)==4 || RuntoBreakFlag(*MapFrame)==11 || RuntoBreakFlag(*MapFrame)==12) && 
//					BreaktoChangeFlag(*MapFrame)<150+185*(*BlockFrame-'0'))
//			{
//				MotionState=MOTION_CHANGE;
//			} 
			
			
			//===============前进方向与测距方向相反时情况===========================
			if(InvDir(*RunFrame)==*MapFrame && 																		//前进方向与测距方向相反，跳过圆弧
				*NextMapFrame!='S' &&	(*ChangeDis - '0') < 6 &&											//排除掉末尾路段情况
				(tempRoadNum != 0 || TempCrushFlag != 1) && 												//排除掉需要撞击的情况(留给下面处理)
//				(*BlockFrame - '0') < 6 &&                                    		//排除掉长距情况
				(InvDir(*NextMapFrame)!=*MapFrame && *NextMapFrame != *MapFrame) && //排除掉180度换向或者方向不变的情况
				(RuntoBreakFlag(*MapFrame)==0 || RuntoBreakFlag(*MapFrame)==4 || RuntoBreakFlag(*MapFrame)==11 || RuntoBreakFlag(*MapFrame)==12) &&	
				TOFSignalFlag(*MapFrame)>2 &&
				BreaktoChangeFlag(*MapFrame)<183+185*(*BlockFrame-'0') &&
				BreaktoChangeFlag(*MapFrame)>147+185*(*BlockFrame-'0'))
			{
				SlowSpeedFlag = 0;//将慢速标志位归零
				MotionState=MOTION_CHANGE;
			}
			
//			//===============前进方向与测距方向相反时情况（长距）=================
//			if(InvDir(*RunFrame)==*MapFrame && 															//前进方向与测距方向相反，跳过圆弧
//				*NextMapFrame!='S' &&	(*ChangeDis - '0') < 6 &&								//排除掉末尾路段情况
//				(tempRoadNum != 0 || TempCrushFlag != 1) && 									//排除掉需要撞击的情况(留给下面处理)
//				(*BlockFrame - '0') >= 6 &&                                   //处理长距情况
//				(RuntoBreakFlag(*MapFrame)==0 || RuntoBreakFlag(*MapFrame)==4 || RuntoBreakFlag(*MapFrame)==11 || RuntoBreakFlag(*MapFrame)==12) &&	
//				TOFSignalFlag(*MapFrame)>2 &&
//				BreaktoChangeFlag(*MapFrame)<168+185*(*BlockFrame-'0') &&
//				BreaktoChangeFlag(*MapFrame)>148+185*(*BlockFrame-'0'))
//			{
//				SlowSpeedFlag = 0;//将慢速标志位归零
//				MotionState=MOTION_CHANGE;
//				SlowSpeedFlag = 0;//这个标志位是为了特殊情况下减速，暂时用不上
//			}
			
			
			

			//=============180度换向或者方向不变时跳过圆弧插补============
			if(
				(*NextMapFrame!='S' &&
				(InvDir(*NextMapFrame)==*MapFrame || *NextMapFrame==*MapFrame)
				) && //上面是跳过圆弧的情况
				*RunFrame != *MapFrame &&
				(tempRoadNum != 0 || TempCrushFlag != 1) && //排除掉需要撞击的情况(留给下面处理)
				(RuntoBreakFlag(*MapFrame)==0 || RuntoBreakFlag(*MapFrame)==4 || RuntoBreakFlag(*MapFrame)==11 || RuntoBreakFlag(*MapFrame)==12) &&	
				TOFSignalFlag(*MapFrame)>2 &&
				BreaktoChangeFlag(*MapFrame)<166+185*(*BlockFrame-'0') &&
				BreaktoChangeFlag(*MapFrame)>144+185*(*BlockFrame-'0'))
			{
				SlowSpeedFlag = 0;//将慢速标志位归零
				MotionState=MOTION_CHANGE;
			}
			
			
			//===============测距距离超过阈值时跳过圆弧插补=============
			if(
				(*NextMapFrame!='S' && 																						//排除掉末尾路段的情况
				(tempRoadNum != 0 || TempCrushFlag != 1) && 											//排除掉需要撞击的情况(留给下面处理)
				(InvDir(*NextMapFrame)!=*MapFrame && *NextMapFrame!=*MapFrame)&&	//排除掉180换向或者方向不变的情况
				InvDir(*RunFrame)!=*MapFrame &&																		//排除掉前进与测距方向反向的情况
				(*ChangeDis - '0') < 6) &&																				//排除掉弧距过长的情况
																																				//上面是跳过圆弧的情况
				(*BlockFrame - '0') >= 6 &&																			
				(RuntoBreakFlag(*MapFrame)==0 || RuntoBreakFlag(*MapFrame)==4 || RuntoBreakFlag(*MapFrame)==11 || RuntoBreakFlag(*MapFrame)==12) &&		
				TOFSignalFlag(*MapFrame)>0 &&
				BreaktoChangeFlag(*MapFrame)>129+185*(*BlockFrame-'0') &&
				BreaktoChangeFlag(*MapFrame)<154+185*(*BlockFrame-'0'))  //这个阈值需要单独调
			{
				SlowSpeedFlag = 0;//将慢速标志位归零
				MotionState=MOTION_CHANGE;
				SlowSpeedFlag = 0;//这个标志位是为了特殊情况下减速
			}
			

			
			//==================处理末尾路段情况========================
			//三种情况：
			//1.末尾路段不动，只是为了转向；
			//2.末尾路段前进，前进方向和测距方向反向；
			//3.到达终点，前进方向和测距方向反向。
			if(*NextMapFrame=='S' && (*ChangeDis - '0') < 6 &&
				(RuntoBreakFlag(*MapFrame)==0 || RuntoBreakFlag(*MapFrame)==4 || RuntoBreakFlag(*MapFrame)==11 || RuntoBreakFlag(*MapFrame)==12) &&
				TOFSignalFlag(*MapFrame)>2 &&
				BreaktoChangeFlag(*MapFrame)<156+185*(*BlockFrame-'0') &&  
				BreaktoChangeFlag(*MapFrame)>132+185*(*BlockFrame-'0')
				)
			{
				SlowSpeedFlag = 0;//将慢速标志位归零
				MotionState=MOTION_CHANGE;
			}

			//===================处理撞击的情况=========================
			if((tempRoadNum == 0 && TempCrushFlag == 1) &&  //处理撞击情况：已经改成直接处理撞击标志位（之前的处理方式是下一帧前进方向和这一帧测距方向相同）
				(*ChangeDis - '0') < 6 && 
				(RuntoBreakFlag(*MapFrame)==0 || RuntoBreakFlag(*MapFrame)==4 || RuntoBreakFlag(*MapFrame)==11 || RuntoBreakFlag(*MapFrame)==12) &&
				TOFSignalFlag(*MapFrame)>2 &&
				BreaktoChangeFlag(*MapFrame)<170+185*(*BlockFrame-'0') &&  
				BreaktoChangeFlag(*MapFrame)>135+185*(*BlockFrame-'0')
			)
			{
				SlowSpeedFlag = 0;//将慢速标志位归零
				MotionState=MOTION_CHANGE;
			}
			
			//===================处理弧距过长的问题=====================
			if(
				((*ChangeDis - '0') >= 6) && 
			(RuntoBreakFlag(*MapFrame)==0 || RuntoBreakFlag(*MapFrame)==4 || RuntoBreakFlag(*MapFrame)==11 || RuntoBreakFlag(*MapFrame)==12) &&
			TOFSignalFlag(*MapFrame)>2 &&
			(InvDir(*NextMapFrame)!=*MapFrame && *NextMapFrame!=*MapFrame) &&
			BreaktoChangeFlag(*MapFrame)<153+185*(*BlockFrame-'0') &&  //可能要改阈值 稍微改大一点
			BreaktoChangeFlag(*MapFrame)>135+185*(*BlockFrame-'0')
			)
			{
				SlowSpeedFlag = 0;//将慢速标志位归零
				MotionState=MOTION_CHANGE;
				
			}
			
			//==============处理仅仅转向的情况===========================
			if(*MapFrame == 'S') MotionState=MOTION_CHANGE;
			
			
//----------------------------------------长距跳过圆弧版本end---------------------------------------------------------------------------------------			
			break;
    }
			case MOTION_CIRCLE://圆弧插补
			{
				SpeedCumulativeCirCle(&speedcum,*MapFrame,*NextMapFrame,*BlockFrame);
				Speed.speedx=speedcum.speedx;
				Speed.speedy=speedcum.speedy;
				if(	(RuntoBreakFlag(*NextMapFrame)==0 || RuntoBreakFlag(*NextMapFrame)==4 || RuntoBreakFlag(*NextMapFrame)==11 || RuntoBreakFlag(*NextMapFrame)==12) &&
						TOFSignalFlag(*MapFrame)>5 &&
						BreaktoChangeFlag(InvDir(*NextMapFrame))>75+185*(*ChangeDis-'0'+1) &&
						BreaktoChangeFlag(InvDir(*NextMapFrame))<175+185*(*ChangeDis-'0'+1))//判断是否需要换向
				{
					MotionState=MOTION_CHANGE;
				}
				//180度换向或者下一步前进时不改变方向的两种情况下直接跳过圆弧插补
				if(InvDir(*NextMapFrame)==*MapFrame || *NextMapFrame==*MapFrame || *RunFrame!=*MapFrame)//180度换向直接跳过圆弧插补
				{
					MotionState=MOTION_CHANGE;
				}
				break;
			}
      case MOTION_CHANGE://换向状态
      {
				
				if(*NextMapFrame=='S' || *MapFrame == 'S') 
				{
					MotionState=MOTION_STOP;
					//摄像头拍照云台转向
//					if			 	(CameraDirPro == 0)		PlatformConAbsAng(INIT_DEGREE);					//测距方向是前，摄像头转向后方
//					else if 	(CameraDirPro == 1)		PlatformConAbsAng(INIT_DEGREE + 9000);	//测距方向是左，摄像头转向右方
//					else if	 	(CameraDirPro == 2)		PlatformConAbsAng(INIT_DEGREE - 18000);	//测距方向是后，摄像头转向前方
//					else if	 	(CameraDirPro == 3)		PlatformConAbsAng(INIT_DEGREE - 9000);  //测距方向是右，摄像头转向左方
					
				}
				else if(tempRoadNum == 0 && TempCrushFlag == 1)  //改成了直接检测撞击标志位
				{
					Speed.speedx=0;
					Speed.speedy=0;
					MotionState=MOTION_RUN;
				}
				else MotionState=MOTION_RUN;
				TempCrushFlag = 0;
				tempRoadNum++;      //路段计数递增
//================================宝藏解析标志轮换==================================
				if			(RoadInfoUpper[0][tempRoadNum] == 0) *RunFrame = 'F';
				else if	(RoadInfoUpper[0][tempRoadNum] == 1) *RunFrame = 'L';
				else if	(RoadInfoUpper[0][tempRoadNum] == 2) *RunFrame = 'B';
				else if	(RoadInfoUpper[0][tempRoadNum] == 3) *RunFrame = 'R';
				else if	(RoadInfoUpper[0][tempRoadNum] == 4) *RunFrame = 'S';
				
				if			(RoadInfoUpper[1][tempRoadNum] == 0) *MapFrame = 'F';
				else if	(RoadInfoUpper[1][tempRoadNum] == 1) *MapFrame = 'L';
				else if	(RoadInfoUpper[1][tempRoadNum] == 2) *MapFrame = 'B';
				else if	(RoadInfoUpper[1][tempRoadNum] == 3) *MapFrame = 'R';
				else if	(RoadInfoUpper[1][tempRoadNum] == 4) *MapFrame = 'S';

				*BlockFrame				= RoadInfoUpper[2][tempRoadNum] + '0';
				*ChangeDis				= RoadInfoUpper[3][tempRoadNum] + '0';

				if			(RoadInfoUpper[0][tempRoadNum + 1] == 0) *NextMapFrame = 'F';
				else if	(RoadInfoUpper[0][tempRoadNum + 1] == 1) *NextMapFrame = 'L';
				else if	(RoadInfoUpper[0][tempRoadNum + 1] == 2) *NextMapFrame = 'B';
				else if	(RoadInfoUpper[0][tempRoadNum + 1] == 3) *NextMapFrame = 'R';
				else if	(RoadInfoUpper[0][tempRoadNum + 1] == 4) *NextMapFrame = 'S';
//================================宝藏解析标志轮换end================================

  

//==============================云台随测距方向转向===================================
//				if 			(*MapFrame == 'F')	PlatformConAbsAng(INIT_DEGREE + 18000);    //记得在协议解析的地方也有摄像头转向
//				else if (*MapFrame == 'L')	PlatformConAbsAng(INIT_DEGREE - 9000);
//				else if (*MapFrame == 'B')	PlatformConAbsAng(INIT_DEGREE);
//				else if (*MapFrame == 'R')	PlatformConAbsAng(INIT_DEGREE + 9000);  
//==============================云台随测距方向转向end===================================
				break;
      }
      case MOTION_STOP://停止状态
      {
        Speed.speedx=0;
        Speed.speedy=0;

//        云台转向程序
//				if(AskNum == 1)
//				{
//					if			 	(RoadInfoUpper[1][RoadsNumUpper - 1] == 0)		PlatformConAbsAng(INIT_DEGREE);					//测距方向是前，摄像头转向后方
//					else if 	(RoadInfoUpper[1][RoadsNumUpper - 1] == 1)		PlatformConAbsAng(INIT_DEGREE + 9000);	//测距方向是左，摄像头转向右方
//					else if	 	(RoadInfoUpper[1][RoadsNumUpper - 1] == 2)		PlatformConAbsAng(INIT_DEGREE + 18000);	//测距方向是后，摄像头转向前方
//					else if	 	(RoadInfoUpper[1][RoadsNumUpper - 1] == 3)		PlatformConAbsAng(INIT_DEGREE - 9000);  //测距方向是右，摄像头转向左方
//				} 

				if(AskNum == 1) 
				{	
					CheckTreasureFlag = 1;//当每条路径第====三十====次进入STOP状态时请求检测宝藏(接收到回复后标志位会清零)
				}		
				AskNum++;							  //防止反复请求检测
				
				if(RoadInfoFinishFlag == 1)//路段信息接收完成
				{
//					RunFrame			= map;
//					MapFrame			=	map+1;				//地图帧中的四位数据都从头调用字符串
//					BlockFrame		=	map+2;				
//					ChangeDis			=	map+3;
//					NextMapFrame	=	map+4;
					tempRoadNum 	= 0;        //路段计数归零
					MotionState=MOTION_RUN;		//调换到开始状态
					AskNum = 0;				      	//进入STOP状态计数归零，准备下一次宝藏检测请求                        。。。再不能用就亖了
				}
				break;
      }
			case MOTION_PAUSE://暂停状态
			{
				Speed.speedx=0;
        Speed.speedy=0;
				if(HAL_GPIO_ReadPin(BLO_GPIO_Port, BLO_Pin) == 0)
				{
					MotionState=MOTION_RUN;	
					PauseBlockFlag = 0;
				}
			
			}
    }
		if(MotionState!=MOTION_INIT) Speed.speedw=-Ang_PID_Absolute(fmod(yaw,360),0);
		else  Speed.speedw=0;
		if(PauseBlockFlag == 0)
		{
			if(HAL_GPIO_ReadPin(BLO_GPIO_Port, BLO_Pin) == 1)
			{
				MotionState=MOTION_PAUSE;
				PauseBlockFlag = 1;
			}
		}
		M2006_motion_vector(Speed.speedx,Speed.speedy,Speed.speedw);
	}
	
	
	
	
	if (htim->Instance == TIM13)
	{
	sendUART();
	}
}

void SpeedCumulativeRun(Speed_t *speed,Liner_t *liner,char dir)
{
  switch(dir){
    case 'F':{
      speed->speedx=StardardSpeed;
      speed->speedy=SpeedOffset(liner->front);
      break;
    }case 'B':{
      speed->speedx=-StardardSpeed;
      speed->speedy=-SpeedOffset(liner->back);
      break;
    }case 'L':{
      speed->speedx=SpeedOffset(liner->left);
      speed->speedy=-StardardSpeed;
      break;
    }case 'R':{
      speed->speedx=-SpeedOffset(liner->right);
      speed->speedy=StardardSpeed;
      break;
    }
  }
}

void SlowSpeedCumulativeRun(Speed_t *speed,Liner_t *liner,char dir)
{
  switch(dir){
    case 'F':{
      speed->speedx=SlowStardardSpeed;
      speed->speedy=SpeedOffset(liner->front);
			//speed->speedy=0;
      break;
    }case 'B':{
      speed->speedx=-SlowStardardSpeed;
      speed->speedy=-SpeedOffset(liner->back);
			//speed->speedy=0;
      break;
    }case 'L':{
      speed->speedx=SpeedOffset(liner->left);
      speed->speedy=-SlowStardardSpeed;
			//speed->speedx=0;
      break;
    }case 'R':{
      speed->speedx=-SpeedOffset(liner->right);
      speed->speedy=SlowStardardSpeed;
			//speed->speedx=0;
      break;
    }
  }
}
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

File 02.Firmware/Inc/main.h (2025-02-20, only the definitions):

#define CS1_GYRO_Pin GPIO_PIN_4
#define CS1_GYRO_GPIO_Port GPIOC
#define CS1_ACCEL_Pin GPIO_PIN_5
#define CS1_ACCEL_GPIO_Port GPIOC
#define R4_Pin GPIO_PIN_13
#define R4_GPIO_Port GPIOF
#define L1_Pin GPIO_PIN_14
#define L1_GPIO_Port GPIOF
#define R3_Pin GPIO_PIN_15
#define R3_GPIO_Port GPIOF
#define L2_Pin GPIO_PIN_0
#define L2_GPIO_Port GPIOG
#define R2_Pin GPIO_PIN_1
#define R2_GPIO_Port GPIOG
#define L3_Pin GPIO_PIN_7
#define L3_GPIO_Port GPIOE
#define R1_Pin GPIO_PIN_8
#define R1_GPIO_Port GPIOE
#define L4_Pin GPIO_PIN_9
#define L4_GPIO_Port GPIOE
#define F4_Pin GPIO_PIN_10
#define F4_GPIO_Port GPIOE
#define B1_Pin GPIO_PIN_11
#define B1_GPIO_Port GPIOE
#define F3_Pin GPIO_PIN_12
#define F3_GPIO_Port GPIOE
#define B2_Pin GPIO_PIN_13
#define B2_GPIO_Port GPIOE
#define F2_Pin GPIO_PIN_14
#define F2_GPIO_Port GPIOE
#define B3_Pin GPIO_PIN_15
#define B3_GPIO_Port GPIOE
#define F1_Pin GPIO_PIN_10
#define F1_GPIO_Port GPIOB
#define B4_Pin GPIO_PIN_11
#define B4_GPIO_Port GPIOB
#define B4G6_Pin GPIO_PIN_6
#define B4G6_GPIO_Port GPIOG
#define BLO_Pin GPIO_PIN_1
#define BLO_GPIO_Port GPIOE

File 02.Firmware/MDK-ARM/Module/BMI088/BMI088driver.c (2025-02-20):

#include "BMI088driver.h"
#include "BMI088reg.h"
#include "BMI088Middleware.h"


fp32 BMI088_ACCEL_SEN = BMI088_ACCEL_3G_SEN;
fp32 BMI088_GYRO_SEN = BMI088_GYRO_2000_SEN;



#if defined(BMI088_USE_SPI)

#define BMI088_accel_write_single_reg(reg, data) \
    {                                            \
        BMI088_ACCEL_NS_L();                     \
        BMI088_write_single_reg((reg), (data));  \
        BMI088_ACCEL_NS_H();                     \
    }
#define BMI088_accel_read_single_reg(reg, data) \
    {                                           \
        BMI088_ACCEL_NS_L();                    \
        BMI088_read_write_byte((reg) | 0x80);   \
        BMI088_read_write_byte(0x55);           \
        (data) = BMI088_read_write_byte(0x55);  \
        BMI088_ACCEL_NS_H();                    \
    }
//#define BMI088_accel_write_muli_reg( reg,  data, len) { BMI088_ACCEL_NS_L(); BMI088_write_muli_reg(reg, data, len); BMI088_ACCEL_NS_H(); }
#define BMI088_accel_read_muli_reg(reg, data, len) \
    {                                              \
        BMI088_ACCEL_NS_L();                       \
        BMI088_read_write_byte((reg) | 0x80);      \
        BMI088_read_muli_reg(reg, data, len);      \
        BMI088_ACCEL_NS_H();                       \
    }

#define BMI088_gyro_write_single_reg(reg, data) \
    {                                           \
        BMI088_GYRO_NS_L();                     \
        BMI088_write_single_reg((reg), (data)); \
        BMI088_GYRO_NS_H();                     \
    }
#define BMI088_gyro_read_single_reg(reg, data)  \
    {                                           \
        BMI088_GYRO_NS_L();                     \
        BMI088_read_single_reg((reg), &(data)); \
        BMI088_GYRO_NS_H();                     \
    }
//#define BMI088_gyro_write_muli_reg( reg,  data, len) { BMI088_GYRO_NS_L(); BMI088_write_muli_reg( ( reg ), ( data ), ( len ) ); BMI088_GYRO_NS_H(); }
#define BMI088_gyro_read_muli_reg(reg, data, len)   \
    {                                               \
        BMI088_GYRO_NS_L();                         \
        BMI088_read_muli_reg((reg), (data), (len)); \
        BMI088_GYRO_NS_H();                         \
    }

static void BMI088_write_single_reg(uint8_t reg, uint8_t data);
static void BMI088_read_single_reg(uint8_t reg, uint8_t *return_data);
//static void BMI088_write_muli_reg(uint8_t reg, uint8_t* buf, uint8_t len );
static void BMI088_read_muli_reg(uint8_t reg, uint8_t *buf, uint8_t len);

#elif defined(BMI088_USE_IIC)


#endif

static uint8_t write_BMI088_accel_reg_data_error[BMI088_WRITE_ACCEL_REG_NUM][3] =
    {
        {BMI088_ACC_PWR_CTRL, BMI088_ACC_ENABLE_ACC_ON, BMI088_ACC_PWR_CTRL_ERROR},
        {BMI088_ACC_PWR_CONF, BMI088_ACC_PWR_ACTIVE_MODE, BMI088_ACC_PWR_CONF_ERROR},
        {BMI088_ACC_CONF,  BMI088_ACC_NORMAL| BMI088_ACC_800_HZ | BMI088_ACC_CONF_MUST_Set, BMI088_ACC_CONF_ERROR},
        {BMI088_ACC_RANGE, BMI088_ACC_RANGE_3G, BMI088_ACC_RANGE_ERROR},
        {BMI088_INT1_IO_CTRL, BMI088_ACC_INT1_IO_ENABLE | BMI088_ACC_INT1_GPIO_PP | BMI088_ACC_INT1_GPIO_LOW, BMI088_INT1_IO_CTRL_ERROR},
        {BMI088_INT_MAP_DATA, BMI088_ACC_INT1_DRDY_INTERRUPT, BMI088_INT_MAP_DATA_ERROR}

};

static uint8_t write_BMI088_gyro_reg_data_error[BMI088_WRITE_GYRO_REG_NUM][3] =
    {
        {BMI088_GYRO_RANGE, BMI088_GYRO_2000, BMI088_GYRO_RANGE_ERROR},
        {BMI088_GYRO_BANDWIDTH, BMI088_GYRO_1000_116_HZ | BMI088_GYRO_BANDWIDTH_MUST_Set, BMI088_GYRO_BANDWIDTH_ERROR},
        {BMI088_GYRO_LPM1, BMI088_GYRO_NORMAL_MODE, BMI088_GYRO_LPM1_ERROR},
        {BMI088_GYRO_CTRL, BMI088_DRDY_ON, BMI088_GYRO_CTRL_ERROR},
        {BMI088_GYRO_INT3_INT4_IO_CONF, BMI088_GYRO_INT3_GPIO_PP | BMI088_GYRO_INT3_GPIO_LOW, BMI088_GYRO_INT3_INT4_IO_CONF_ERROR},
        {BMI088_GYRO_INT3_INT4_IO_MAP, BMI088_GYRO_DRDY_IO_INT3, BMI088_GYRO_INT3_INT4_IO_MAP_ERROR}

};

uint8_t BMI088_init(void)
{
    uint8_t error = BMI088_NO_ERROR;
    // GPIO and SPI  Init .
    BMI088_GPIO_init();
    BMI088_com_init();

    error |= bmi088_accel_init();
    error |= bmi088_gyro_init();

    return error;
}

bool_t bmi088_accel_init(void)
{
    uint8_t res = 0;
    uint8_t write_reg_num = 0;

    //check commiunication
    BMI088_accel_read_single_reg(BMI088_ACC_CHIP_ID, res);
    BMI088_delay_us(BMI088_COM_WAIT_SENSOR_TIME);
    BMI088_accel_read_single_reg(BMI088_ACC_CHIP_ID, res);
    BMI088_delay_us(BMI088_COM_WAIT_SENSOR_TIME);

    //accel software reset
    BMI088_accel_write_single_reg(BMI088_ACC_SOFTRESET, BMI088_ACC_SOFTRESET_VALUE);
    BMI088_delay_ms(BMI088_LONG_DELAY_TIME);

    //check commiunication is normal after reset
    BMI088_accel_read_single_reg(BMI088_ACC_CHIP_ID, res);
    BMI088_delay_us(BMI088_COM_WAIT_SENSOR_TIME);
    BMI088_accel_read_single_reg(BMI088_ACC_CHIP_ID, res);
    BMI088_delay_us(BMI088_COM_WAIT_SENSOR_TIME);

    // check the "who am I"
    if (res != BMI088_ACC_CHIP_ID_VALUE)
    {
        return BMI088_NO_SENSOR;
    }

    //set accel sonsor config and check
    for (write_reg_num = 0; write_reg_num < BMI088_WRITE_ACCEL_REG_NUM; write_reg_num++)
    {

        BMI088_accel_write_single_reg(write_BMI088_accel_reg_data_error[write_reg_num][0], write_BMI088_accel_reg_data_error[write_reg_num][1]);
        BMI088_delay_us(BMI088_COM_WAIT_SENSOR_TIME);

        BMI088_accel_read_single_reg(write_BMI088_accel_reg_data_error[write_reg_num][0], res);
        BMI088_delay_us(BMI088_COM_WAIT_SENSOR_TIME);

        if (res != write_BMI088_accel_reg_data_error[write_reg_num][1])
        {
            return write_BMI088_accel_reg_data_error[write_reg_num][2];
        }
    }
    return BMI088_NO_ERROR;
}
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

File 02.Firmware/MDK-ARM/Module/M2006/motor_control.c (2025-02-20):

#include "bsp_can.h"
#include "pid.h"
#include "stm32f4xx_hal.h"

PID_TypeDef motor_pid[4];


void motor_init_4p(void)
{
//	filter_to_can_1();
	filter_to_can_2();
	for(int i=0; i<4; i++)
	{	
		pid_init(&motor_pid[i]);
		motor_pid[i].f_param_init(&motor_pid[i],PID_Speed,16384,5000,10,0,8000,0,1.5,0.1,0); 
	}
}

void M2006_motion_vector(int x_speed,int y_speed,int turn_speed)
{
	//麦轮位置解算
	motor_pid[0].target = 0 + x_speed + y_speed + turn_speed;  
	motor_pid[1].target = 0 + x_speed - y_speed + turn_speed;
	motor_pid[2].target = 0 - x_speed - y_speed + turn_speed;
	motor_pid[3].target = 0 - x_speed + y_speed + turn_speed;
	
	//速度环PID（根据设定值进行PID计算）
	motor_pid[0].f_cal_pid(&motor_pid[0],moto_chassis[0].speed_rpm);   
	motor_pid[1].f_cal_pid(&motor_pid[1],moto_chassis[1].speed_rpm);   
	motor_pid[2].f_cal_pid(&motor_pid[2],moto_chassis[2].speed_rpm);   
	motor_pid[3].f_cal_pid(&motor_pid[3],moto_chassis[3].speed_rpm);   
	
	//将PID的计算结果通过CAN发送到电机
	set_moto_current(&hcan2, motor_pid[0].output,  
							 motor_pid[1].output,
                             motor_pid[2].output,
                             motor_pid[3].output);
}

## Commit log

2024-11-14 提交测试
2024-11-14 迁入04.结构件的全部文件
    [0.28寸3位数码管.SLDPRT, 3.5寸屏幕.SLDPRT, 3mm_bolt.SLDPRT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]
2024-11-15 迁入03.电路板的全部文件
    [PM06-2304-电调中央板.PrjPcb, PM06-2305-IMU小板.PcbDoc, PM06-2305-IMU小板.PrjPcb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]
2025-02-20 迁入02固件的全部文件，增加readme的团队信息
2025-02-20 更新readme
2025-02-24 迁入01.Sofrware的全部文件，以仓库引用
2025-02-24 更新半决赛视频
2025-02-24 精简电路板部分
    [PM06-保险杠灯-V1.step, main.SchDoc, 实用电路-STM32F407ZET6最小系统板.PrjPcb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]
2025-02-25 删除了一些历史多余文件
2025-02-26 修复#1

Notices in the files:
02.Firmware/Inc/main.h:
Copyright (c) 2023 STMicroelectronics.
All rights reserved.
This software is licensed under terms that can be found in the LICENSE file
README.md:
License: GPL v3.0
